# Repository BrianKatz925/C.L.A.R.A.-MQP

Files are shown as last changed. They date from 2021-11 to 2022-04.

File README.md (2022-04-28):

# C.L.A.R.A.-MQP

This is the GitHub repository for the 2021-22 CLARA MQP.

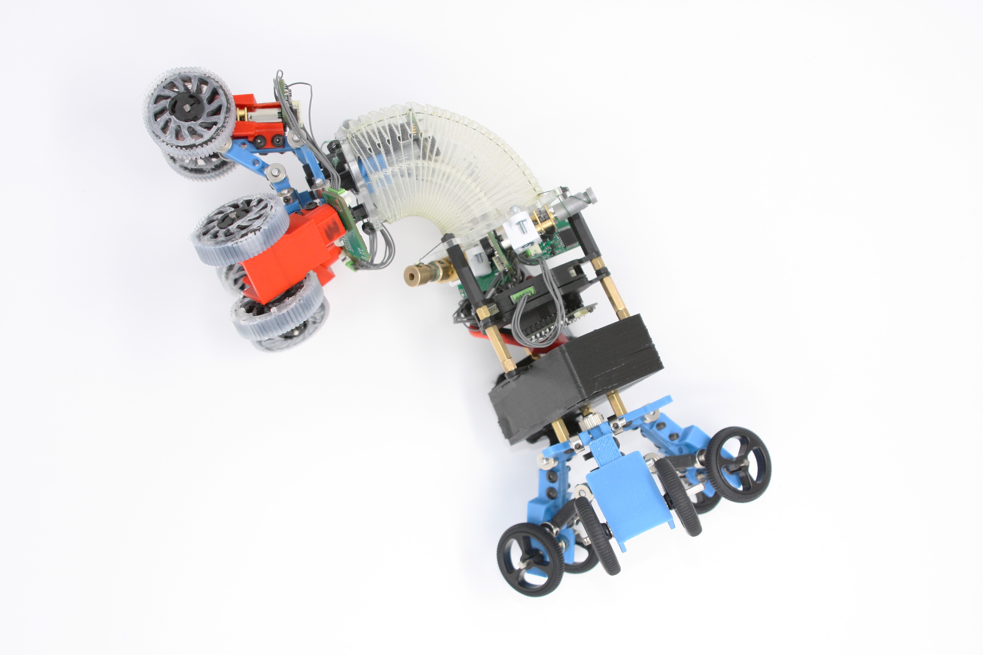
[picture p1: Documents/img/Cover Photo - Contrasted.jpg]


## Navigating the Repository
There are three main sections to the CLARA repository. 
  1. The first is the [Code](Code/) section, which contains all of the code used for the CLARA robot. Please refer to the [README](Code/README.md) in that section for more information on operation and code organization.
  2. The next is the [Documents](Documents/) section. In here, you can find all of the deliverables (presentation, report, etc.) and important planning documents used throughout our project.
  3. The last is the [Mechanical + Electrical Files](https://github.com/BrianKatz925/C.L.A.R.A.-MQP/tree/master/Mechanical%20%2B%20Electrical%20Files) section, which includes the Solidworks parts/assemblies, STLs, DXFs, and Altium Designer project files for the PCBs. Please refer to the [README](https://github.com/BrianKatz925/C.L.A.R.A.-MQP/blob/master/Mechanical%20%2B%20Electrical%20Files/README.md) in that section for more information on organization schema of the mechanical and electrical files.

Enjoy :)



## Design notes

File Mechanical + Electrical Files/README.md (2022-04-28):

# C.L.A.R.A.-MQP

This section contains all of the electrical and mechanical files for the 2021-22 CLARA MQP

## Navigating the this section
### PCB Files
In the [Altium](https://github.com/BrianKatz925/C.L.A.R.A.-MQP/tree/master/Mechanical%20%2B%20Electrical%20Files/Altium) section, you can find all iterations of the Mainboard and Smart Motor Driver PCB. The [Version 4 folder](https://github.com/BrianKatz925/C.L.A.R.A.-MQP/tree/master/Mechanical%20%2B%20Electrical%20Files/Altium/Version%204) contains the most updated version of each board.
  1. In the Version 4 folder, the main documents are the [CLARA Mainboard folder](https://github.com/BrianKatz925/C.L.A.R.A.-MQP/tree/master/Mechanical%20%2B%20Electrical%20Files/Altium/Version%204/CLARA%20Mainboard) and the [updated_sami_board_v3 folder](https://github.com/BrianKatz925/C.L.A.R.A.-MQP/tree/master/Mechanical%20%2B%20Electrical%20Files/Altium/Version%204/updated_sami_board%20v3/updated_sami_board).
  2. To import both of these files, along with other files in the design project in Altium, use the [Revision 4 12.24.2021.DsnWrk](https://github.com/BrianKatz925/C.L.A.R.A.-MQP/blob/master/Mechanical%20%2B%20Electrical%20Files/Altium/Version%204/Revision%204%2012.24.2021.DsnWrk) which will open up the design project group in Altium.

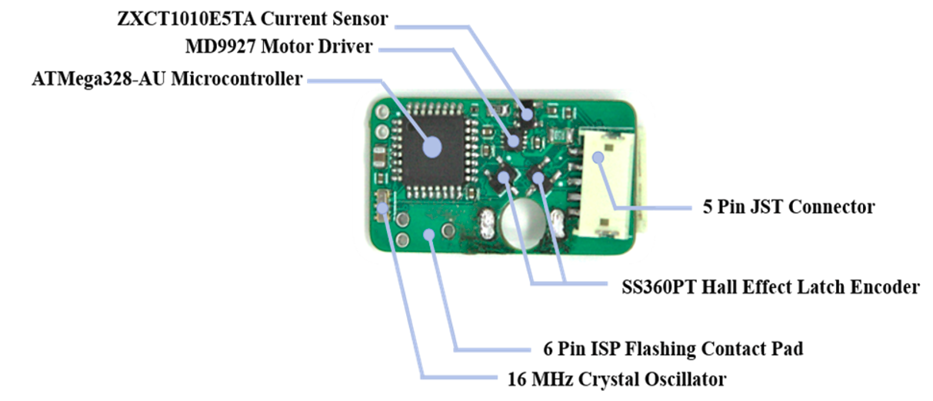
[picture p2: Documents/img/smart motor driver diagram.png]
|  | 
|:--:| 
| *Smart Motor Driver Diagram* |

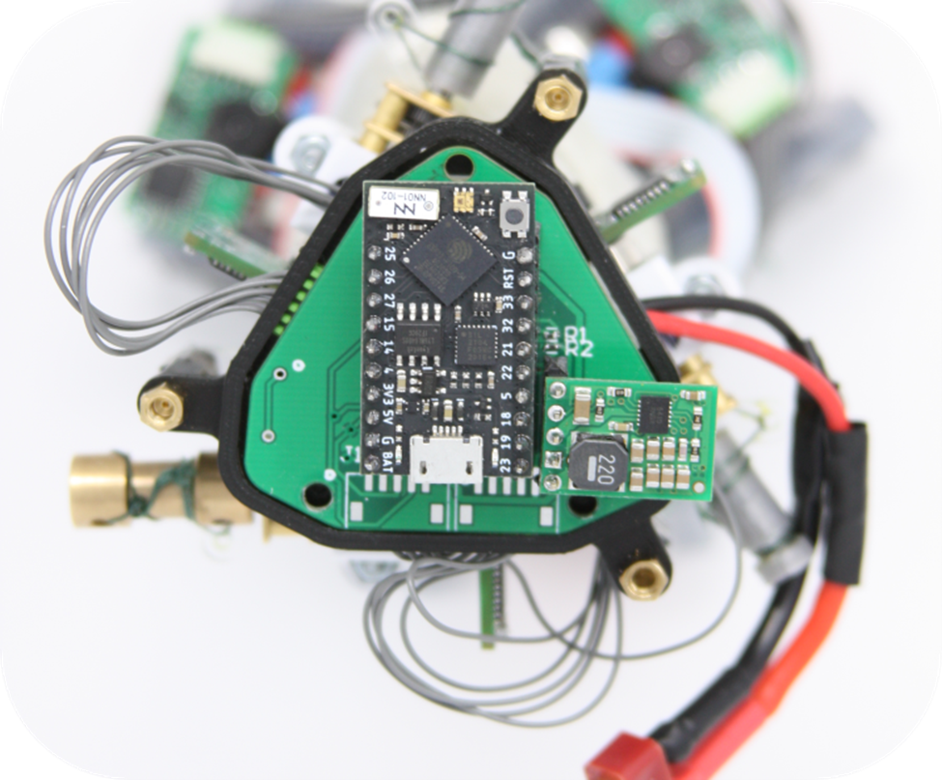
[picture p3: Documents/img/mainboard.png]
|  | 
|:--:| 
| *CLARA Mainboard* |

### Solidworks Files
In the [Salamander Assembly](https://github.com/BrianKatz925/C.L.A.R.A.-MQP/tree/master/Mechanical%20%2B%20Electrical%20Files/Salamander%20Assembly) folder, you will find the [Final CLARA Assembly](https://github.com/BrianKatz925/C.L.A.R.A.-MQP/blob/master/Mechanical%20%2B%20Electrical%20Files/Salamander%20Assembly/Final%20CLARA%20Assembly.ziphttps://github.com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) zip file, which is a pack-and-go from the final Solidworks Assembly.
  1. There is also a folder called [Final Version](https://github.com/BrianKatz925/C.L.A.R.A.-MQP/tree/master/Mechanical%20%2B%20Electrical%20Files/Salamander%20Assembly/Final%20Version) which contains some STL files as well. We recommend unzipping the pack-and-go as all files are included properly there.
  2. The [Alternative Version folder](https://github.com/BrianKatz925/C.L.A.R.A.-MQP/tree/master/Mechanical%20%2B%20Electrical%20Files/Salamander%20Assembly/Alternative%20Version) features our CAM-slide mechanism.
  3. The [Wheel Files folder](https://github.com/BrianKatz925/C.L.A.R.A.-MQP/tree/master/Mechanical%20%2B%20Electrical%20Files/Salamander%20Assembly/Wheel%20Files) features our wheel molds to create the TPU/Silicone compression wheels.
  4. Lastly, the [STL](https://github.com/BrianKatz925/C.L.A.R.A.-MQP/tree/master/Mechanical%20%2B%20Electrical%20Files/Salamander%20Assembly/STL) folder contains some of the STL files we used throughout the project for 3D printing.

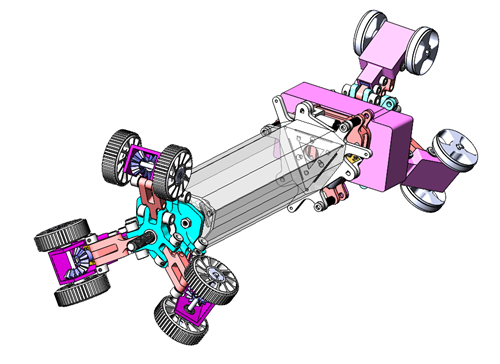
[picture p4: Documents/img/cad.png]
|  | 
|:--:| 
| *Final CAD Assembly of the CLARA Robot* |

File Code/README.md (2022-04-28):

# C.L.A.R.A.-MQP

This is the GitHub repository for the 2021-22 CLARA MQP.

## Instructions
### Prerequisites

1. Complete the prerequisites of the [CLARA-Gamepad Repository](https://github.com/phonymacoroni/CLARA-Gamepad).
2. Connect an ESP32 device (ESP32DevKitC, TinyPICO, etc.) to a USB port on your computer, this will be referred as the external ESP.
4. Upload the [`mac_address.ino` code](TinyPICO_Sender_Code/mac_address) to the external ESP and open the Serial Monitor, write down the MAC address.
5. Locate the [robotcode folder](robotcode), which contains the code required to operate the robot.
6. In the `pico_master.ino` and `inverse_kinematics_pico_master.ino` file, replace the current MAC address with that of the external ESP.
7. Connect the TinyPICO that will be going into the mainboard and retrieve its MAC address by repeating step 3.
8. In the `pico_sender.ino` and `inverse_kinematics_esp_sender.ino` files, replace the current MAC address with that of your TinyPICO.
9. For normal robot operation, upload the `pico_sender.ino code` to the external ESP and the `pico_master.ino` code to the mainboard TinyPICO.
10. For inverse kinematics demonstration, upload the `inverse_kinematics_esp_sender.ino` code to the external ESP and the `inverse_kinematics_pico_master.ino` to the mainboard TinyPICO.

### Operation
#### Typical Robot Operation
Typical Robot Operation requires the use of an external Logitech Gamepad as the form of input.

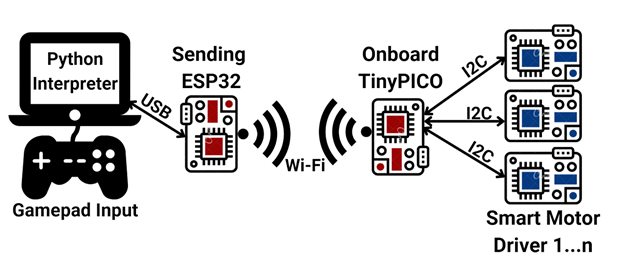
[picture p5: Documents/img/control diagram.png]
|  | 
|:--:| 
| *CLARA Operation Control Diagram* |

Refer to the control protocol for the Gamepad below:

| Input  | WiFi Sender Command  | I2C Status Command | Smart Motor Driver Action |
|:---:|:---:|:-----:|:-----:|
| Default | "0" | 0 | Brake all motors | 
| Y Button | "1" | 1 | Rotate lead screw (0x07) - increase diameter |
| X Button | "2" | N/A | Request encoder, current sensor, motor rpm data from all motors |
| A Button | "4" | 2 | Rotate lead screw (0x07) - decrease diameter |
| Right Bumper | "8" | 8 | Drive wheel motors forward - fast speed |
| Left Bumper | "9" | 9 | Drive wheel motors reverse - fast speed |
| DPad 0 (North) | "10" | 0 | Brake all motors - homing |
| DPad 1 (Northeast) | "11" | N/A | Decrease all cable lengths |
| DPad 2 (East) | "12" | Cable 1: 12, <br />Cable 2: 0, <br />Cable 3: 0 | Decrease cable 1 (0x04) length |
| DPad 3 (Southeast) | "13" | Cable 1: 12, <br />Cable 2: 12, <br />Cable 3: 0 | Decrease cable 1 (0x04) and cable 2 (0x05) length |
| DPad 4 (South) | "14" | Cable 1: 0, <br />Cable 2: 12, <br />Cable 3: 0 | Decrease cable 2 (0x05) length |
| DPad 5 (Southwest) | "15" | Cable 1: 0, <br />Cable 2: 12, <br />Cable 3: 12 | Decrease cable 2 (0x05) and cable 3 (0x06) length |
| DPad 6 (West) | "16" | Cable 1: 0, <br />Cable 2: 0, <br />Cable 3: 12 | Decrease cable 3 (0x06) length |
| DPad 7 (Northwest) | "17" | N/A | Increase all cable lengths |
| B Button + D Pad 2 | "18" | Cable 1: 13, <br />Cable 2: 0, <br />Cable 3: 0 | Increase cable 1 (0x04) length |
| B Button + D Pad 4 | "19" | Cable 1: 0, <br />Cable 2: 13, <br />Cable 3: 0 | Increase cable 2 (0x05) length |
| B Button + D Pad 6 | "20" | Cable 1: 0, <br />Cable 2: 0, <br />Cable 3: 13 | Increase cable 3 (0x06) length |
| B Button + Right Bumper | "21" | 10 | Drive wheel motors forward - PID slow speed |
| B Button + Right Bumper | "22" | 11 | Drive wheel motors reverse - PID slow speed|
| A Button + Right Bumper | "23" | 3 | Rotate lead screw (0x07) - decrease diameter until current limit |
| Y  Button + Right Bumper | "24" | 4 | Rotate lead screw (0x07) - increase diameter until current limit|

#### Inverse Kinematics Demonstration
The Gamepad can be disconnected with this demonstration.

Instead the Serial Monitor is used to input values for the configuration parameters **S** (arc length), **theta** (bending angle), and **phi** (rotation about z-axis).

The bounds for each variable are defined in the `inverse_kinematics_esp_sender.ino` file.

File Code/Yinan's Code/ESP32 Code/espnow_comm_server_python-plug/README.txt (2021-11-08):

Upload to the external ESP32 as the sender of messages

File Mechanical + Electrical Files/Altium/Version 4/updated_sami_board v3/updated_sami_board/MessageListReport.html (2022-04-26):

Altium customize

# Message List

Date: | | 10/12/2021
Time: | | 12:13:04 PM
Elapsed Time: | | 00:00:00

Class | Document | Source | Message | Time | Date | No.
Situs Event | sami_updated.PcbDoc | Situs | Routing Started | 12:12:19 PM | 10/12/2021 | 1
Routing Status | sami_updated.PcbDoc | Situs | Creating topology map | 12:12:19 PM | 10/12/2021 | 2
Situs Event | sami_updated.PcbDoc | Situs | Starting Fan out to Plane | 12:12:19 PM | 10/12/2021 | 3
Situs Event | sami_updated.PcbDoc | Situs | Completed Fan out to Plane in 0 Seconds | 12:12:19 PM | 10/12/2021 | 4
Situs Event | sami_updated.PcbDoc | Situs | Starting Memory | 12:12:19 PM | 10/12/2021 | 5
Situs Event | sami_updated.PcbDoc | Situs | Completed Memory in 0 Seconds | 12:12:19 PM | 10/12/2021 | 6
Situs Event | sami_updated.PcbDoc | Situs | Starting Layer Patterns | 12:12:19 PM | 10/12/2021 | 7
Routing Status | sami_updated.PcbDoc | Situs | Calculating Board Density | 12:12:19 PM | 10/12/2021 | 8
Situs Event | sami_updated.PcbDoc | Situs | Completed Layer Patterns in 0 Seconds | 12:12:19 PM | 10/12/2021 | 9
Situs Event | sami_updated.PcbDoc | Situs | Starting Main | 12:12:19 PM | 10/12/2021 | 10
Routing Status | sami_updated.PcbDoc | Situs | 58 of 60 connections routed (96.67%) in 19 Seconds 1 contention(s) | 12:12:38 PM | 10/12/2021 | 11
Situs Event | sami_updated.PcbDoc | Situs | Completed Main in 19 Seconds | 12:12:39 PM | 10/12/2021 | 12
Situs Event | sami_updated.PcbDoc | Situs | Starting Completion | 12:12:39 PM | 10/12/2021 | 13
Routing Status | sami_updated.PcbDoc | Situs | 59 of 60 connections routed (98.33%) in 34 Seconds | 12:12:53 PM | 10/12/2021 | 14
Situs Event | sami_updated.PcbDoc | Situs | Completed Completion in 14 Seconds | 12:12:53 PM | 10/12/2021 | 15
Situs Event | sami_updated.PcbDoc | Situs | Starting Straighten | 12:12:53 PM | 10/12/2021 | 16
Routing Status | sami_updated.PcbDoc | Situs | 59 of 60 connections routed (98.33%) in 35 Seconds | 12:12:54 PM | 10/12/2021 | 17
Situs Event | sami_updated.PcbDoc | Situs | Completed Straighten in 1 Second | 12:12:55 PM | 10/12/2021 | 18
Routing Status | sami_updated.PcbDoc | Situs | 59 of 60 connections routed (98.33%) in 36 Seconds | 12:12:55 PM | 10/12/2021 | 19
Situs Event | sami_updated.PcbDoc | Situs | Routing finished with 0 contentions(s). Failed to complete 1 connection(s) in 36 Seconds | 12:12:55 PM | 10/12/2021 | 20

Back to top

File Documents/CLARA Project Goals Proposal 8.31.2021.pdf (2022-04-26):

MQP Meeting #1
8.31.2021
Overview:
We would like to focus on primarily mechanical and electrical improvements to the existing salamander robot such that we can create a robot with the following specifications capable of performing the below demonstrations. Additionally, we would like to tailor the improvements and constraints in order to qualify the robot for the NASA Big Idea Challenge, and work with another MQP team as necessary in order to meet the mechanical, electrical, and controls requirements of the challenge.

Areas of Interest:
- Improved suspension system. Want to use either a passively or actively deformable suspension system to make the robot capable of traversing multiple sized tubes
- Improved PCB design. Want a new PCB design that is smaller overall (whether that be through enhanced PCB space allocation or a foldable/flexible board) and allows us to scale down the size of the body
- Viability of smaller body with either the Yoshimura pattern or another folding pattern still capable of deforming linearly while maintaining the present level of torsional stiffness
- Integrating usage of robot with vine soft robot for deployment purposes as well as making the salamander usable in wet/humid environments
- Making robot usable in both vacuum and pressurized environments

Specifications:
- Size
- Robot should be able to be used within a 3” SCH STD pipe
■ Due to schedule piping, the ID of a 2” ND pipe would be below 2” and the 3” ND pipe will be >2”.
- Robot is usable in pipes up to 6” nominal for vertical climbs
- Speed
- Robot is able to travel at a reasonable pace (this will be hardware dependant)
- Mobility
- Robot should meet a 90 degree minimum turning radius
- Robot should be able to traverse a 90 degree incline in a pipe
- Robot should be able to climb at least a 30 degree slope.
- Robot should be able to traverse pipe with constrictions/expansion
■ This would be doable with an active suspension, not so much with a passive unless we have enough force to really push the robot forward to where the suspension system buckles inward
- Sensing
- Robot should be, at minimum, able to integrate a camera at the robot head for navigation/inspection/sample collection purposes
- We’re gonna need other sensing? Temperature and Pressure sensors might be good and easy, if we care about mapping the space this gets more complex
- Other
- Robot should be able to deploy a small scientific payload ( idk what size that really means here)

■ This might mean we have to have a modular design of the robot, so that we can have a scoop or something to collect regolith

Demonstrations:
- Within clear pipe
- General locomotion
■ Forwards, turning, etc.
- Passage through a t-split
■ Choose which direction to take instead of following flow
- Locomotion through varying inclines (45, 60, 90?)
■ Within pipes and potentially up stairs
- Traverse a constriction
- Bridge a gap
■ To deploy the robot into a pipe inlet without human assistance
- Deployment with vine robot
- Can we actually get our hands on one? It may be hard to really demonstrate this otherwise
- Payload deployment

Questions
- Budget
- If our budget is low, do you have any recommendations for receiving funding?
- Lab space/equipment
- Do we have a dedicated lab space (Soft Robotics Lab), if so can we get Kate access?
- Start to set calendar/Gantt chart with major deadlines that we currently know of

A Term Goals
By end of A term we have:
- Made it through rapid prototyping phase of suspension mechanism - pursued at least 3 designs and tested physical models
- Gives us an outline for the overall maximum size and flexibility of the robot
- Have landed on a solution/have a solid plan for the smaller PCB. Doesn’t have to be completed, but we must land on a path forward
- Talk to Dan Moyer - get a consultation on the feasibility of a foldable/flexible PCB and what connections may be subtracted
- Will give minimum size
- Have a viable solution to the smaller body. Have either produced a smaller body with the current folding pattern or have found another solution.
- This will outline the minimum size

Other notes:
With regards to NASA challenge
- Market and sell robot as being good in steep and rugged slopes and for subterranean features (especially caves and lava tubes)
- Required:
- Needs to be able to manage intrusion of dust
- Be cost effective
- Low barrier to adoption. (i.e. low mass, small, low power, reliable)
- Desired
- Able to autonomously navigate through hazardous environments
- Able to transport objects with larger mass than it’s own

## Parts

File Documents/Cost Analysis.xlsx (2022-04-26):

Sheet: Sheet1
Category | Part Name | Quantity | Unit Cost | Extended Cost
Body
 | PET Sheet | 36"x10" sheet | $0.00 | $0.00
 | PowerPro 50lb fishing line | 18" | $20.00 | $0.03
 | Cable Winches | 3 | $0.00 | $0.00
 | Acrylic Mounting Plates | 2 | $0.00 | $0.00
 | Motor Brackets | 3 | $3.95 | $11.85
Suspension
 | 3D Printed Parts | - | $0.00 | $0.00
 | 5mm Ball Bearing | 3 | $1.00 | $3.00
 | 5mm Shaft Collar | 3 | $0.78 | $2.35
 | M5 Lead Screw (4") | 1 | $0.00 | $0.00
 | M3 Shaft Collar | 30 | $0.27 | $7.99
 | M3 Assorted Screw Kit | 1 | $10.98 | $10.98
 | 3mm Ball Bearing | 12 | $1.70 | $20.38
 | 3mm D Shaft | 20" | $0.00 | $0.00
 | Standoffs | 12 | $0.00 | $0.00
 | Dragonskin | 0.25 bottle | $0.00 | $0.00
 | Pololu Wheels | 12 | $1.48 | $17.70
Electronics
 | 1:150 N20 Gearmotor | 1 | $3.00 | $3.00
 | 1:298 N20 Gearmotor | 6 | $23.45 | $140.70
 | Smart Motor Drivers (components incl) | 7 | $9.32 | $65.23
 | Mainboard (components incl) | 1 | $34.08 | $34.08
 | Tiny Pico | 1 | $20.00 | $20.00
 | Buck Regulator | 1 | $6.95 | $6.95
 | ESP 32 | 1 | $9.00 | $9.00
 | 12 CPR Encoder Disks | 7 | $2.00 | $14.00
 | LiPo Battery | 1 | $10.95 | $10.95
 | 6 pin pogo connector | 1 | $33.95 | $33.95
 | Logitech Gamepad | 1 | $16.39 | $16.39
 | 6 cable JST connectors | 7 | $1.59 | $11.13
Total |  |  |  | $439.65

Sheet: Smart Motor Driver
Part Name | Qty ordered | total cost | cost per component | components per board | cost per board
PCB Board | 10 | $5.00 | $0.50 | 1 | $0.50
ATMega328-AU | 25 | $79.10 | $3.16 | 1 | $3.16
SS360PT Hall Effect Sensor | 20 | $22.20 | $1.11 | 2 | $2.22
MD9927 Motor Driver | 30 | $5.19 | $0.17 | 1 | $0.17
ZXCT1010E5TA Current Sensor | 30 | $22.51 | $0.75 | 1 | $0.75
GRM155R71C104KA88D 0.1 uF capacitor | 50 | $1.10 | $0.02 | 6 | $0.13
CSTNE16M0V53C000R0 16 MHz oscillator | 20 | $5.46 | $0.27 | 1 | $0.27
GRM21BR61E106KA73L 10 uF capacitor | 25 | $7.30 | $0.29 | 1 | $0.29
ERJ-1GNF1002C - 10 kOhm Resistor | 25 | $1.33 | $0.05 | 1 | $0.05
RL1220S-R50-F - 0.5 Ohm Resistor | 25 | $6.08 | $0.24 | 1 | $0.24
ERA-3AEB122V - 1.2 kOhm Resistor | 25 | $7.48 | $0.30 | 1 | $0.30
S5B-ZR-SM4A-TF(LF)(SN) 5 pin JST connector | 50 | $30.46 | $0.61 | 2 | $1.22
 |  |  |  | Total | $9.32

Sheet: Mainboard
Part Name | Qty ordered | total cost | cost per component | components per board | cost per board
PCB Board | 5 | $5.00 | $1.00 | 1 | $1.00
S5B-ZR-SM4A-TF(LF)(SN) 5 pin JST connector | 50 | $30.46 | $0.61 | 9 | $5.48
TinyPICO ESP32 Microcontroller | 3 | $60.00 | $20.00 | 1 | $20.00
D24V10F3 - 3.3 Buck Regulator | 2 | $14.98 | $7.49 | 1 | $7.49
RMCF0402JT4K70 - 10kOhm Resistor | 25 | $1.33 | $0.05 | 2 | $0.11
Dean's Connector | 5 | $9.49 | $1.90 | 2 | $3.80
 |  |  |  | Total | $34.08

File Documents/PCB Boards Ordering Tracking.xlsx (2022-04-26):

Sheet: Big Old - Sami
Component # | Description | QTY per board | Stock | Cost | Link | Total Required | Total Cost | Potential Replacement?
TLE4946-2K | Hall Effect Sensor | 2 | 384 | 0.27 - must buy all 384 | https://www.rocelec.com/part/inftle4946-2k |  |  | https://www.mouser.com/ProductDetail/Honeywell/SS360PT?qs=I6adikXrXuA6SFyXzjBzBQ%3D%3D
ATTINY2313V-10MU | 8-bit Microcontroller 18 I/O Pins | 1 | 1139 | 1.96 | https://www.mouser.com/ProductDetail/Microchip-Technology-Atmel/ATTINY2313V-10MU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
LT1999IMS8-20#PBF | Current Sense Amplifiers | 1 | 0 | 5.84 | https://www.mouser.com/ProductDetail/Analog-Devices/LT1999IMS8-20PBF?qs=ytflclh7QUVh4hf%252BhdZY6Q%3D%3D |  |  | 27 available from SRL
SM05B-GHS-TB(LF)(SN) | JST | 2 | 1707 | 0.5 | https://lcsc.com/product-detail/Wire-To-Board-Wire-To-Wire-Connector_JST-Sales-America-SM05B-GHS-TB-LF-SN_C189896.html

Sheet: 104 - Sami
Component # | Description | QTY per board | Stock | Cost | Link | Total Required | Total Cost | Potential Replacement?
SS360PT | Digital Hall Effect Sensor | 2 | 7062 | 1.7 | https://www.mouser.com/ProductDetail/Honeywell/SS360PT?qs=I6adikXrXuA6SFyXzjBzBQ%3D%3D
A3910EEETR-T | Half Bridge (2) DC Brushed Motor Driver | 1 | 11938 | 0.68 | https://www.digikey.com/en/products/detail/allegro-microsystems/A3910EEETR-T/3973532
? | 100 mOhm Resistor | 1 | - | -
INA2180A1IDGKR | Current Sense Amplifier | 1 | 3857 | 0.71 | https://www.mouser.com/ProductDetail/Texas-Instruments/INA2180A1IDGKR?qs=j%252B1pi9TdxUZfv9X7r5aZLA%3D%3D
GRM155R71C104KA88D | 0.1 uF Capacitor | 4 | 840141 | 0.1 | https://www.mouser.com/ProductDetail/Murata-Electronics/GRM155R71C104KA88D?qs=8YPuuxuUzMJKePo9sU3A2g%3D%3D
SM05B-GHS-TB(LF)(SN) | JST Connector | 2 | 1342 | 0.1747 | https://lcsc.com/product-detail/Wire-To-Board-Wire-To-Wire-Connector_JST-Sales-America-SM05B-GHS-TB-LF-SN_C189896.html
ATtiny2313V-10MU | 8 bit microcontroller | 1 | 1139 | 2.08 | https://www.mouser.com/ProductDetail/Microchip-Technology-Atmel/ATTINY2313V-10MU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
CSTNE16M0V53C000R0 | 16MHz Crystal | 1 | 43962 | 0.33 | https://www.digikey.com/en/products/detail/murata-electronics/CSTNE16M0V53C000R0/8747730

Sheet: 106 - Sami
Component # | Description | QTY per board | Stock | Cost | Link | Total Required | Total Cost | Potential Replacement?
SS360PT | Digital Hall Effect Sensor | 2 | 7062 | 1.7 | https://www.mouser.com/ProductDetail/Honeywell/SS360PT?qs=I6adikXrXuA6SFyXzjBzBQ%3D%3D
A3910EEETR-T | Half Bridge (2) DC Brushed Motor Driver | 1 | 11938 | 0.68 | https://www.digikey.com/en/products/detail/allegro-microsystems/A3910EEETR-T/3973532
INA2180A1IDGKR | Current Sense Amplifier | 1 | 3857 | 0.71 | https://www.mouser.com/ProductDetail/Texas-Instruments/INA2180A1IDGKR?qs=j%252B1pi9TdxUZfv9X7r5aZLA%3D%3D
GRM155R71C104KA88D | 0.1 uF Capacitor | 5 | 840141 | 0.1 | https://www.mouser.com/ProductDetail/Murata-Electronics/GRM155R71C104KA88D?qs=8YPuuxuUzMJKePo9sU3A2g%3D%3D
SM05B-GHS-TB(LF)(SN) | JST Connector | 2 | 1342 | 0.1747 | https://lcsc.com/product-detail/Wire-To-Board-Wire-To-Wire-Connector_JST-Sales-America-SM05B-GHS-TB-LF-SN_C189896.html
ATMEGA328-AU | 8 bit microcontroller | 1 | 2151 | 2.18 | https://www.mouser.com/ProductDetail/Microchip-Technology-Atmel/ATMEGA328-AU?qs=lwdSMh1%2FoYJRHuGBjWz9Pg%3D%3D | https://store.arduino.cc/products/arduino-nano
CSTNE16M0V53C000R0 | 16MHz Crystal | 1 | 43962 | 0.33 | https://www.digikey.com/en/products/detail/murata-electronics/CSTNE16M0V53C000R0/8747730
RL1220S-R10-F | 100 mOhm Resistor | 1 | 27890 | 0.29 | https://www.digikey.com/en/products/detail/susumu/RL1220S-R10-F/432480
JMF212AB7106KGHT | 10 uF Capacitor | 1 | 94430 | 0.3 | https://www.mouser.com/ProductDetail/Taiyo-Yuden/JMF212AB7106KGHT?qs=GedFDFLaBXGIGsv8E%252BcpMQ%3D%3D
ERJ-1GNF1002C - 10kOhm | 10 kOhm Resistor | 1 | 888637 | 0.1 | https://www.digikey.com/en/products/detail/panasonic-electronic-components/ERJ-1GNF1002C/2036226

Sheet: 106 - Mainboard
Component # | Description | QTY per board | Stock | Cost | Link | Total Required | Total Cost | Potential Replacement?
TinyPICO | ESP32 Controller | 1 | 1 | 20 | https://www.adafruit.com/product/4335 | 1 | 20
NCV1117ST50T3G | 5V Voltage Regulator | 1 | 6298 | 0.61 | https://www.digikey.com/en/products/detail/on-semiconductor/NCV1117ST50T3G/1967231 | 1
SM05B-GHS-TB(LF)(SN) | JST Connector | 9 | 837 | 0.17 | https://lcsc.com/product-detail/Wire-To-Board-Wire-To-Wire-Connector_JST-Sales-America-SM05B-GHS-TB-LF-SN_C189896.html | 9
NCP1117DT33T5G | 3.3V Voltage Regulator | 1 | 37696 | 0.58 | https://www.digikey.com/en/products/detail/onsemi/NCP1117DT33T5G/921285 | 1
JMF212AB7106KGHT | 10 uF Capacitor | 4 | 94430 | 0.3 | https://www.mouser.com/ProductDetail/Taiyo-Yuden/JMF212AB7106KGHT?qs=GedFDFLaBXGIGsv8E%252BcpMQ%3D%3D | 4
BM02B-SRSS-TB (LF)(SN) | 2 pin JST Connector | 1 | 36697 | 0.48 | https://www.digikey.com/en/products/detail/jst-sales-america-inc/BM02B-SRSS-TB-LF-SN/926694 | 1

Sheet: 1010 - Sami
Component # | Description | QTY per board | Stock | Cost | Link | In Hand
SS360PT | Digital Hall Effect Sensor | 2 | 7062 | 1.7 | https://www.mouser.com/ProductDetail/Honeywell/SS360PT?qs=I6adikXrXuA6SFyXzjBzBQ%3D%3D
A3910EEETR-T | Half Bridge (2) DC Brushed Motor Driver | 1 | 11938 | 0.68 | https://www.digikey.com/en/products/detail/allegro-microsystems/A3910EEETR-T/3973532 | 10
INA2180A1IDGKR | Current Sense Amplifier | 1 | 3857 | 0.71 | https://www.mouser.com/ProductDetail/Texas-Instruments/INA2180A1IDGKR?qs=j%252B1pi9TdxUZfv9X7r5aZLA%3D%3D
GRM155R71C104KA88D | 0.1 uF Capacitor | 7 | 840141 | 0.1 | https://www.mouser.com/ProductDetail/Murata-Electronics/GRM155R71C104KA88D?qs=8YPuuxuUzMJKePo9sU3A2g%3D%3D
S5B-ZR-SM4A-TF(LF)(SN) | JST Connector - ZR Family | 2 | 25147 | 0.1747 | https://www.digikey.com/en/products/detail/jst-sales-america-inc/S5B-ZR-SM4A-TF-LF-SN/926603
ATMEGA328-AU | 8 bit microcontroller | 1 | 2151 | 2.18 | https://www.mouser.com/ProductDetail/Microchip-Technology-Atmel/ATMEGA328-AU?qs=lwdSMh1%2FoYJRHuGBjWz9Pg%3D%3D
CSTNE16M0V53C000R0 | 16MHz Crystal | 1 | 43962 | 0.33 | https://www.digikey.com/en/products/detail/murata-electronics/CSTNE16M0V53C000R0/8747730 | 10
GRM21BR61E106KA73L | 10 uF Capacitor | 1 | 2941945 | 0.42 | https://www.digikey.com/en/products/detail/murata-electronics/GRM21BR61E106KA73L/2334874
ERJ-1GNF1002C - 10kOhm | 10 kOhm Resistor | 1 | 888637 | 0.1 | https://www.digikey.com/en/products/detail/panasonic-electronic-components/ERJ-1GNF1002C/2036226 | 25
RL1220S-R27-F | 0.27 Ohm Resistor | 1 | 270043 | 0.29 | https://www.digikey.com/en/products/detail/susumu/RL1220S-R27-F/714262 | 0

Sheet: 1010 - Mainboard
Component # | Description | QTY per board | Stock | Cost | Link | Total Required | In Hand
TinyPICO | ESP32 Controller | 1 | 1 | 20 | https://www.adafruit.com/product/4335 | 1
S5B-ZR-SM4A-TF(LF)(SN) | JST Connector - ZR Family | 9 | 25147 | 0.1747 | https://www.digikey.com/en/products/detail/jst-sales-america-inc/S5B-ZR-SM4A-TF-LF-SN/926603 | 9
NCP1117DT33T5G | 3.3V Voltage Regulator | 1 | 37696 | 0.58 | https://www.digikey.com/en/products/detail/onsemi/NCP1117DT33T5G/921285 | 1 | 5
GRM21BR61E106KA73L | 10 uF Capacitor | 2 | 2941945 | 0.42 | https://www.digikey.com/en/products/detail/murata-electronics/GRM21BR61E106KA73L/2334874 | 4 | 25
BM02B-SRSS-TB (LF)(SN) | 2 pin JST Connector | 1 | 36697 | 0.48 | https://www.digikey.com/en/products/detail/jst-sales-america-inc/BM02B-SRSS-TB-LF-SN/926694 | 1 | 10
RMCF0402JT4K70 | 4.7 kOhm Resistor | 2 |  | 0.1 | https://www.digikey.com/en/products/detail/stackpole-electronics-inc/RMCF0402JT4K70/1758241 |  | 25
A05ZR05ZR28H102A | JST ZR Cable - 4" | 10 | 9389 | 1.38 | https://www.digikey.com/en/products/detail/A05ZR05ZR28H102A/455-4306-ND/9972177?so=72195384
A05ZR05ZR28H305B | JST ZR Cable - 12" | 5 | 578 | 1.88 | https://www.digikey.com/en/products/detail/A05ZR05ZR28H305B/455-4249-ND/6708565?so=72195384

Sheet: Things Left To Order
Component # | Description | QTY per board | Stock | Cost | Link | Total Required | In Hand
TC2030-IDC-NL | 6 Pin Spring Loaded Flashing Cable | 1 |  | 33.95 | https://www.tag-connect.com/product/tc2030-idc-nl | 1
Lithium Ion Battery - 3.7v 2000mAh |  | 1 |  | 12.5 | https://www.adafruit.com/product/2011 | 1

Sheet: 1121 - SAMI
Component # | Description | QTY per board | Stock | Cost | Link | In Hand | Reimbursement Sent? | Future Order | Ordered? | Reimbursement Sent?
SS360PT | Digital Hall Effect Sensor | 2 | 6886 | 1.7 | https://www.mouser.com/ProductDetail/Honeywell/SS360PT?qs=I6adikXrXuA6SFyXzjBzBQ%3D%3D | 20 | Yes | 10
GRM155R71C104KA88D | 0.1 uF Capacitor | 7 | 1526282 | 0.1 | https://www.mouser.com/ProductDetail/Murata-Electronics/GRM155R71C104KA88D?qs=8YPuuxuUzMJKePo9sU3A2g%3D%3D | 50 | Yes | 50
S5B-ZR-SM4A-TF(LF)(SN) | JST Connector - ZR Family | 2 | 22893 | 0.1747 | https://www.digikey.com/en/products/detail/jst-sales-america-inc/S5B-ZR-SM4A-TF-LF-SN/926603 | 25 | Yes | 20
ATMEGA328-AU | 8 bit microcontroller | 1 | 0 Fuck Chip Shortage | 2.18 | https://www.mouser.com/ProductDetail/Microchip-Technology-Atmel/ATMEGA328-AU?qs=lwdSMh1%2FoYJRHuGBjWz9Pg%3D%3D | 10 | Yes | 15 | Yes from RFQ | No
CSTNE16M0V53C000R0 | 16MHz Crystal | 1 | 0 | 0.33 | https://www.digikey.com/en/products/detail/murata-electronics/CSTNE16M0V53C000R0/8747730 | 10 | Yes | 12 | Yes | No
GRM21BR61E106KA73L | 10 uF Capacitor | 1 | 2941945 | 0.42 | https://www.digikey.com/en/products/detail/murata-electronics/GRM21BR61E106KA73L/2334874 | 25 | Yes | No
ERJ-1GNF1002C - 10kOhm | 10 kOhm Resistor | 1 | 888637 | 0.1 | https://www.digikey.com/en/products/detail/panasonic-electronic-components/ERJ-1GNF1002C/2036226 | 25 | Yes | No
---------
MD9927 | H-Bridge Motor Driver supports 8.4V | 1 | 27 | 0.25 | https://www.lcsc.com/product-detail/Motor-Driver-ICs_Shanghai-Mingda-Microelectronics-MD9927_C2684662.html | 0 | No | 30 | Yes | No
ZXCT1010E5TA | Current Sense Amplifier - 20 V | 1 | 20 | 1.04 | https://www.lcsc.com/product-detail/Current-Sensing-Amplifiers_Diodes-Incorporated-ZXCT1010E5TA_C14151.html | 0 | No | 30 | Yes | No
ERA-3AEB122V | 1.2KOhm Resistor - 1/10W 0603 | 1 | 55813 | 0.32 | https://www.digikey.com/en/products/detail/panasonic-electronic-components/ERA-3AEB122V/1465856 | 0 | No | 30
RL1220S-R50-F | 0.5 Ohm Resistor - 1/3W 0805 | 1 | 2957 | 0.29 | https://www.digikey.com/en/products/detail/susumu/RL1220S-R50-F/567251 | 0 | No | 30

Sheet: 1121 Mainboard
Component # | Description | QTY per board | Stock | Cost | Link | In Hand | Reimbursement Request Sent? | Future Order
TinyPICO | ESP32 Controller | 1 | 1 | 20 | https://www.adafruit.com/product/4335 | 2 | Yes
S5B-ZR-SM4A-TF(LF)(SN) | JST Connector - ZR Family | 9 | 22893 | 0.1747 | https://www.digikey.com/en/products/detail/jst-sales-america-inc/S5B-ZR-SM4A-TF-LF-SN/926603 | 25 | Yes | 20
GRM21BR61E106KA73L | 10 uF Capacitor | 2 | 2941945 | 0.42 | https://www.digikey.com/en/products/detail/murata-electronics/GRM21BR61E106KA73L/2334874 | 25 | Yes | 30
BM02B-SRSS-TB (LF)(SN) | 2 pin JST Connector | 1 | 36697 | 0.48 | https://www.digikey.com/en/products/detail/jst-sales-america-inc/BM02B-SRSS-TB-LF-SN/926694 | 10 | Yes | No
RMCF0402JT4K70 | 4.7 kOhm Resistor | 2 | 1947472 | 0.1 | https://www.digikey.com/en/products/detail/stackpole-electronics-inc/RMCF0402JT4K70/1758241 | 25 | Yes | No
A05ZR05ZR28H102A | JST ZR Cable - 4" | 10 | 9389 | 1.38 | https://www.digikey.com/en/products/detail/A05ZR05ZR28H102A/455-4306-ND/9972177?so=72195384 | 10 | Yes | No
A05ZR05ZR28H305B | JST ZR Cable - 12" | 5 | 578 | 1.88 | https://www.digikey.com/en/products/detail/A05ZR05ZR28H305B/455-4249-ND/6708565?so=72195384 | 5 | Yes | No
Lithion Ion Battery 3.7V + Micro USB Charger |  | 1 | - | 31.32 |  | 1 | No | No
Tag Connect 6 Pin ISP Connector |  | 1 |  | 33.95 |  | 1 | No | No
---
D24V10F3 | Pololu 3.3V Buck Switching Regulator Module | 1 | 81 | 7.49 | https://www.pololu.com/product/2830 | 0 |  | 2

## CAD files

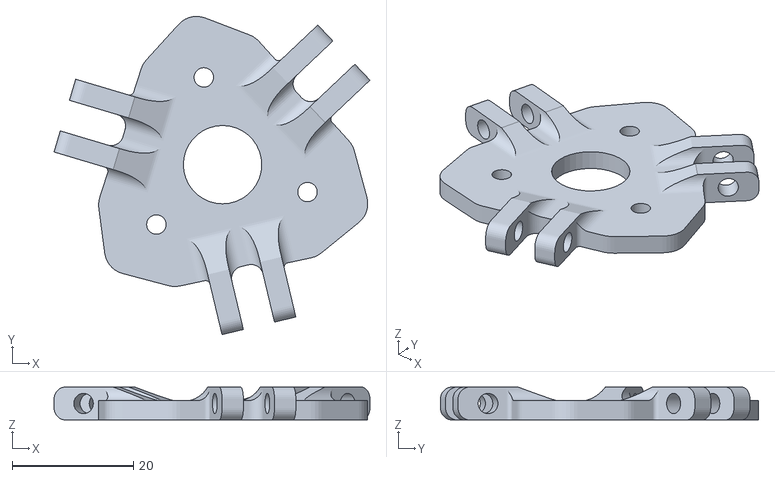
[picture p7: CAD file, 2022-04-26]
Mechanical + Electrical Files/Salamander Assembly/Final Version/STL/Bottom Link Faceplate^Salamander Assembly.STL
52.0 x 52.4 x 5.43

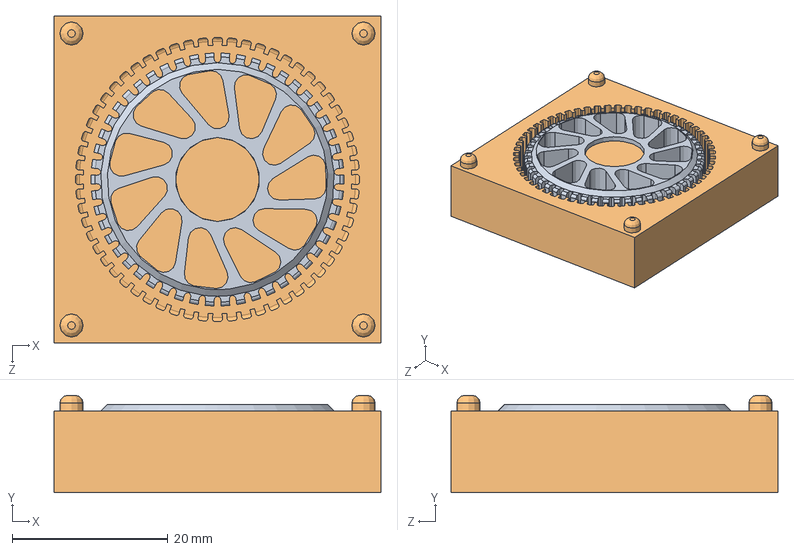
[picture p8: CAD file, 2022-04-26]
Mechanical + Electrical Files/Salamander Assembly/Wheel Files/Mold v2/Moldyv2.SLDASM
42.0 x 12.5 x 42.0 mm
COmpression Wheel v5
Cavityv2

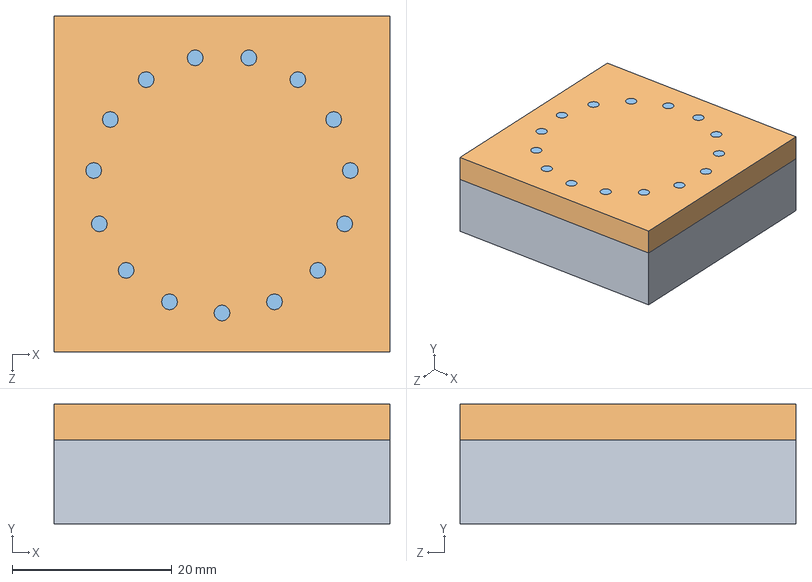
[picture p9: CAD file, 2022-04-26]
Mechanical + Electrical Files/Salamander Assembly/Wheel Files/Mold v2/Mold Assemv2.SLDASM
42.0 x 14.9 x 42.0 mm
Cavityv2
Cavity No Cavityv2

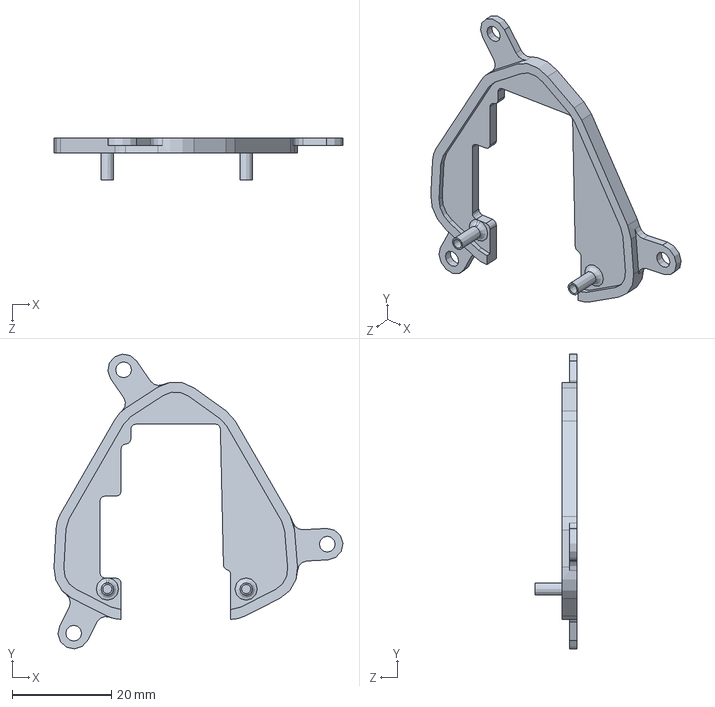
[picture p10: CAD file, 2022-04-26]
Mechanical + Electrical Files/Salamander Assembly/Final Version/Mainboard Shell Top.SLDPRT
58.3 x 59.5 x 8.50 mm

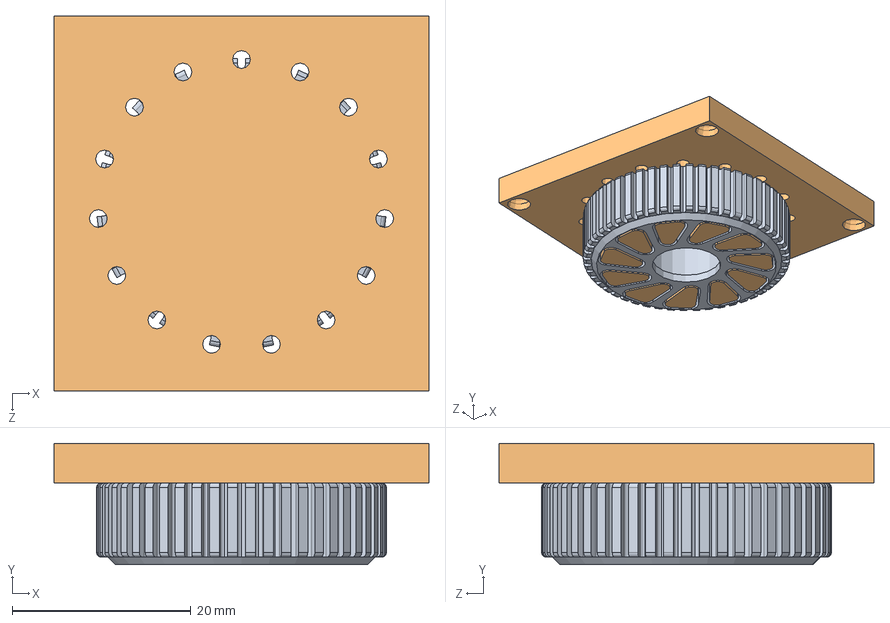
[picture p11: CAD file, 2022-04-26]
Mechanical + Electrical Files/Salamander Assembly/Wheel Files/Mold v2/Moldy2v2.SLDASM
42.0 x 13.6 x 42.0 mm

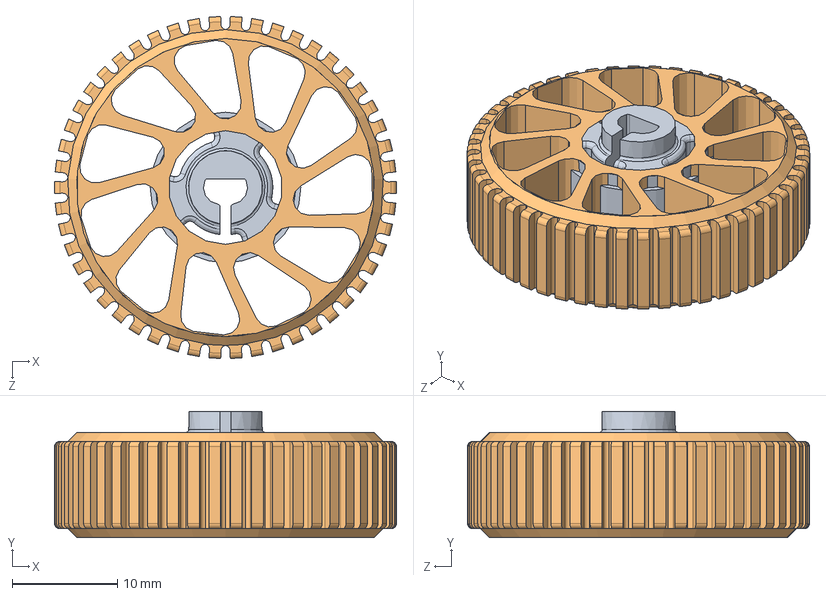
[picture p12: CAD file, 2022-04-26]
Mechanical + Electrical Files/Salamander Assembly/Wheel Files/Compression Wheel v6.SLDASM
32.5 x 12.0 x 32.5 mm
Outer Wheel v3
COmpression Wheel v5

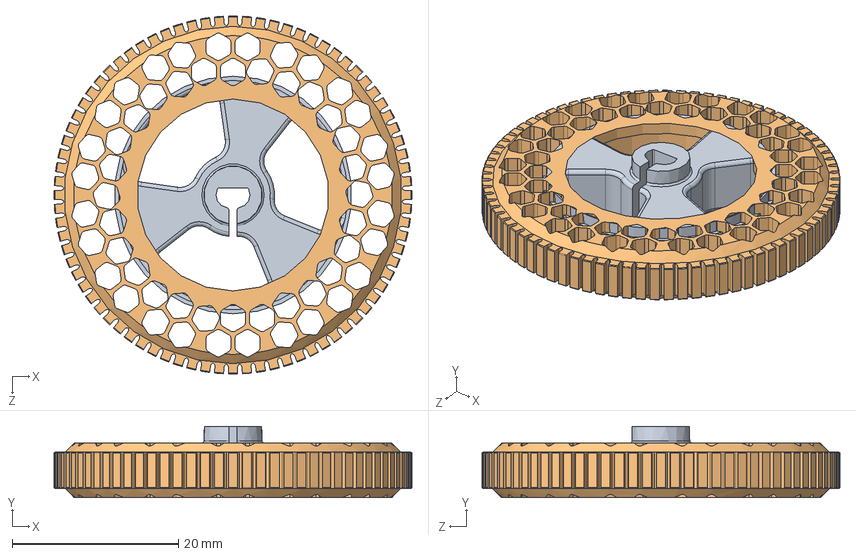
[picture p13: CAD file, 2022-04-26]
Mechanical + Electrical Files/Salamander Assembly/Wheel Files/Compression Wheel.SLDASM
43.1 x 8.60 x 43.1 mm
Outer Wheel
Part1^Compression Wheel

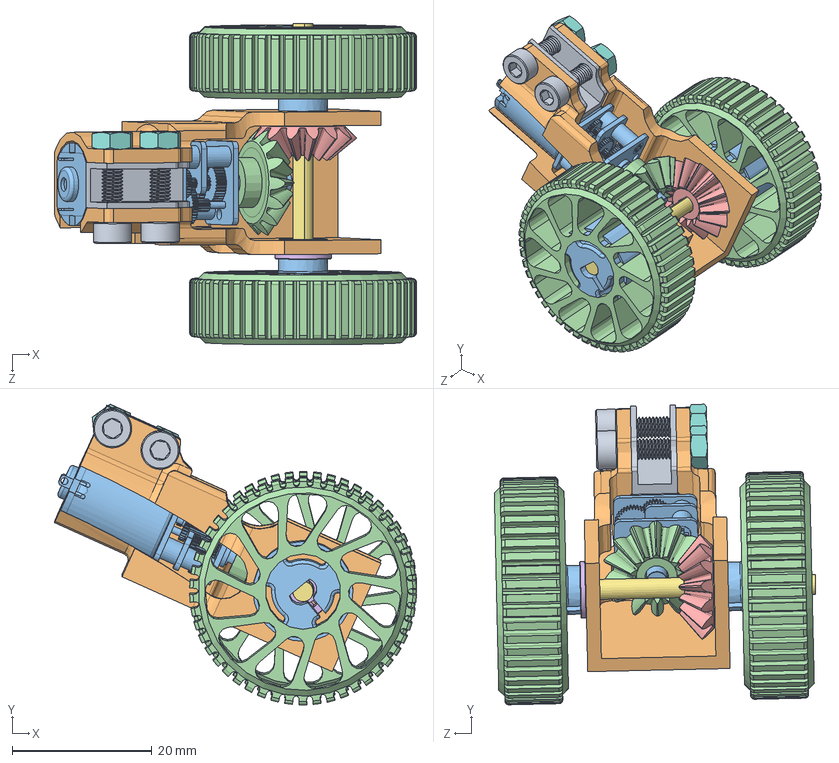
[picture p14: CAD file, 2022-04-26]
Mechanical + Electrical Files/Salamander Assembly/Alternative Version/Motor Housing 1.SLDASM
51.8 x 43.1 x 46.0 mm
Motor Base2
Motor Mount
micro-metal-gearmotor
With_convex-Metric - Straight miter gear 1M14T 20PA 5FW
Metric - Straight miter gear 1M14T 20PA 5FW ---14O10H8MD2N
57155K427_Stainless Steel Ball Bearing x 2
Dshaftd3l40
90592A085_STEEL HEX NUT x 2
91290A115_Black-Oxide Alloy Steel Socket Head Screw x 2
Bevel Gear Spacer
Outer Wheel v3 x 2
COmpression Wheel v5 x 2

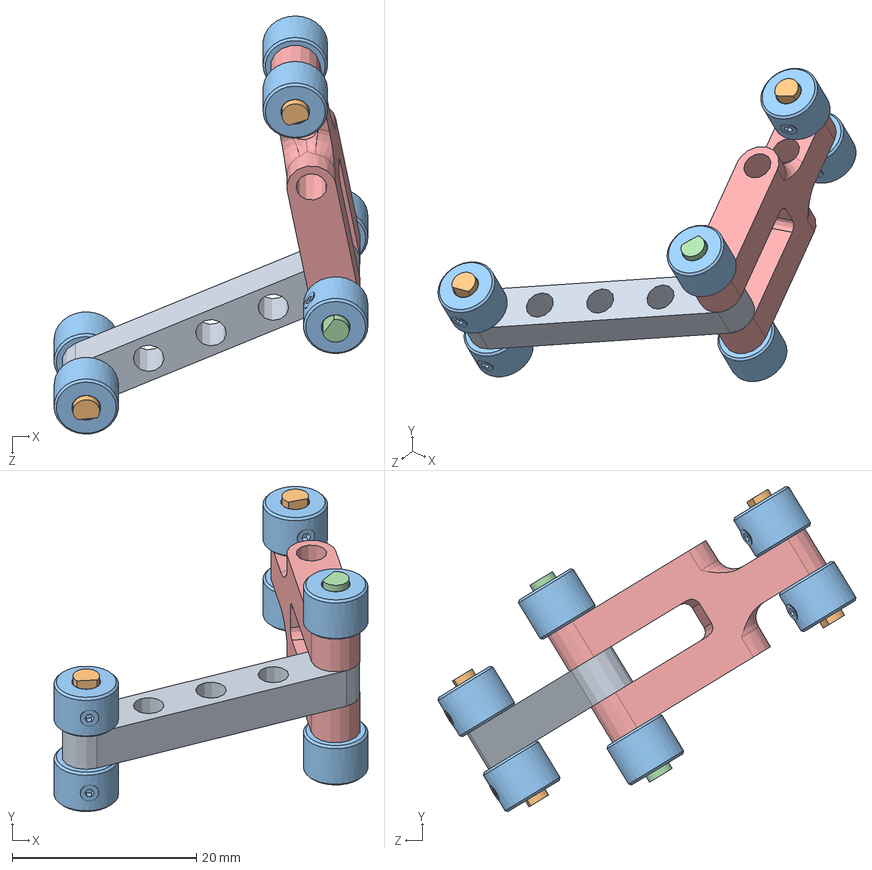
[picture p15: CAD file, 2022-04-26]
Mechanical + Electrical Files/Salamander Assembly/Final Version/Link Assembly.SLDASM
34.1 x 35.3 x 45.4 mm
Base Link
Aluminum D Shaft x 2
6056N11_Carbon Steel Set Screw Collar x 6
Link D Shaft
Upper Link

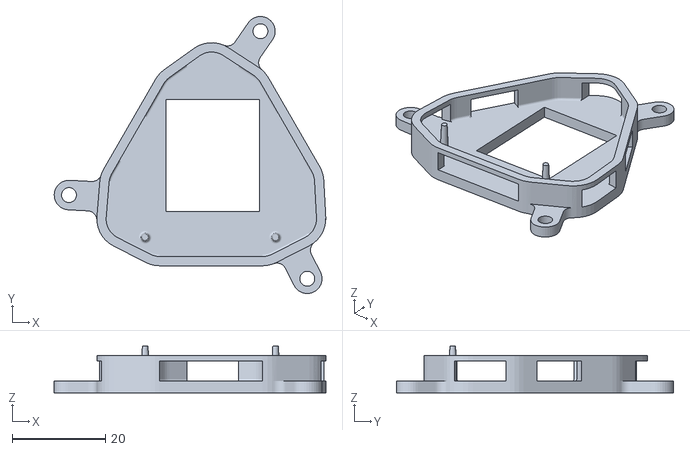
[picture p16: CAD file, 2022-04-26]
Mechanical + Electrical Files/Salamander Assembly/STL/Mainboard Shell Bottom.STL
58.3 x 59.5 x 10.0

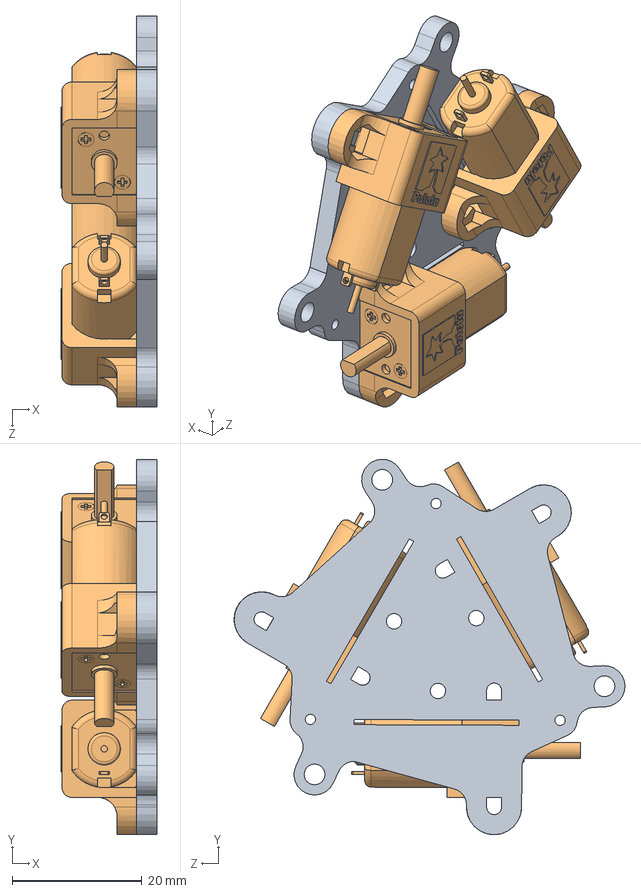
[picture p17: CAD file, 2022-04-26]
Mechanical + Electrical Files/Salamander Assembly/Final Version/Expansion Motor Mount.SLDASM
14.9 x 57.9 x 60.3 mm
motor_mounting_plate_v2
micro-metal-gearmotor-extended-with-1086-bracket x 3

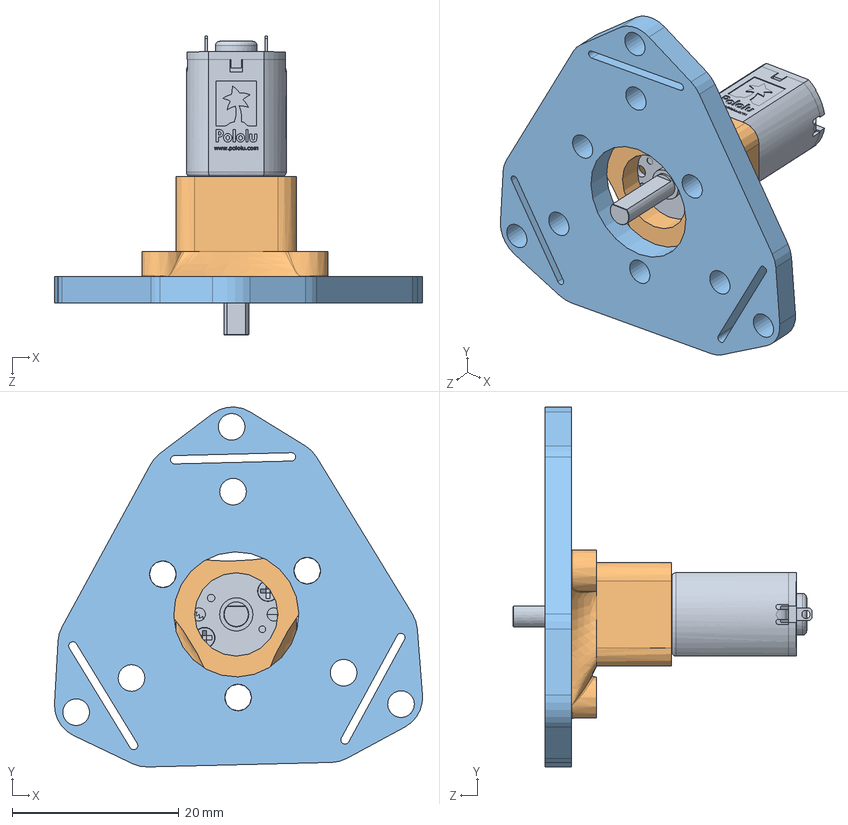
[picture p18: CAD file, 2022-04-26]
Mechanical + Electrical Files/Salamander Assembly/Alternative Version/Motor Flange.SLDASM
44.1 x 43.2 x 35.8 mm
micro-metal-gearmotor
Motor Flange
Top Acrylic Base

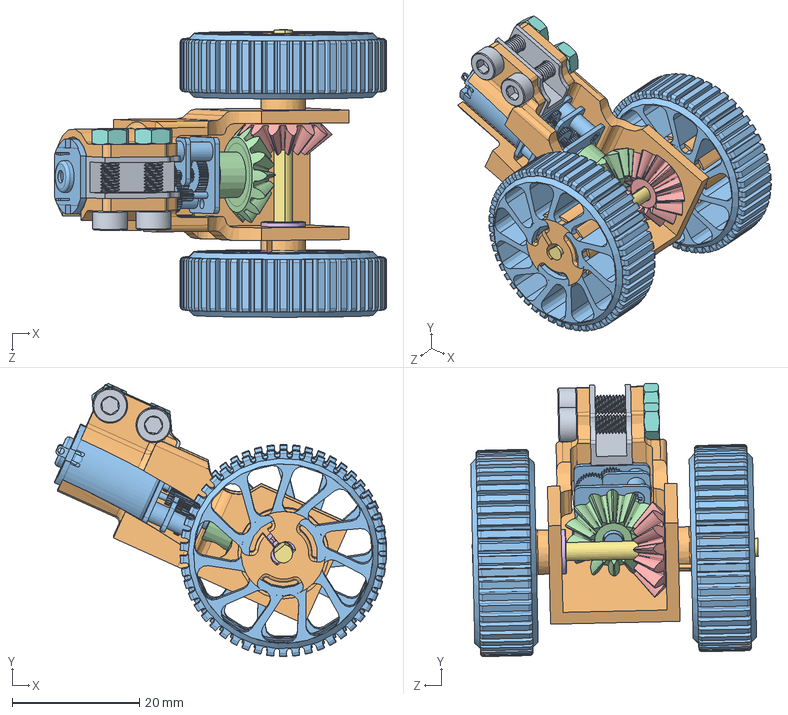
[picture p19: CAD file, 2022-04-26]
Mechanical + Electrical Files/Salamander Assembly/Final Version/Motor Housing 1.SLDASM
52.3 x 43.0 x 45.3 mm
Motor Base2
Motor Mount
micro-metal-gearmotor
With_convex-Metric - Straight miter gear 1M14T 20PA 5FW
Metric - Straight miter gear 1M14T 20PA 5FW ---14O10H8MD2N
57155K427_Stainless Steel Ball Bearing x 2
Dshaftd3l40
90592A085_STEEL HEX NUT x 2
91290A115_Black-Oxide Alloy Steel Socket Head Screw x 2
Outer Wheel v3 x 2
COmpression Wheel v5 x 2

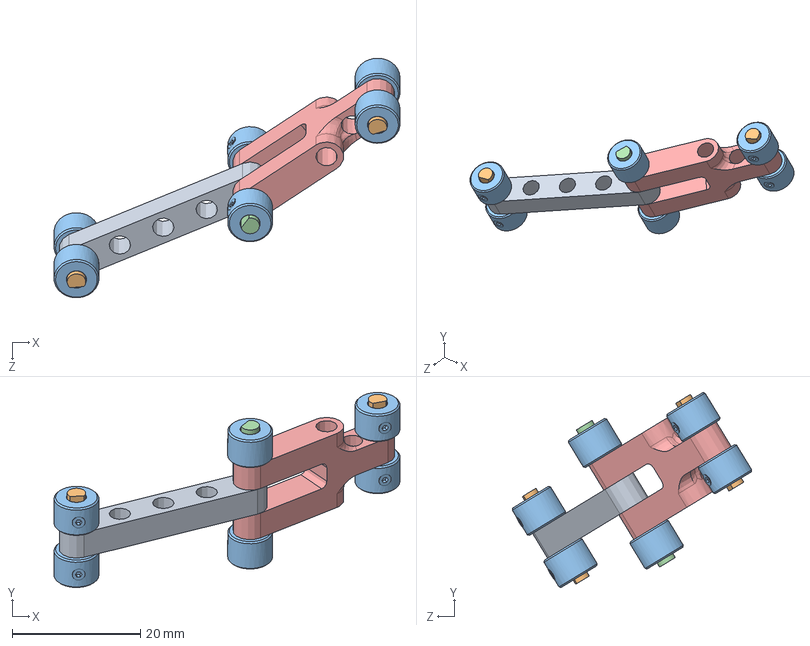
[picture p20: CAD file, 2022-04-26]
Mechanical + Electrical Files/Salamander Assembly/Alternative Version/Link Assembly.SLDASM
53.9 x 30.4 x 37.3 mm
Base Link
Aluminum D Shaft x 2
6056N11_Carbon Steel Set Screw Collar x 6
Link D Shaft
Upper Link

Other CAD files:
Mechanical + Electrical Files/Salamander Assembly/STL/Mainboard Shell Top.STL
Mechanical + Electrical Files/Salamander Assembly/Alternative Version/Top Wheel Housing.SLDASM
Mechanical + Electrical Files/Salamander Assembly/Final Version/Mainboard Shell Bottom.SLDPRT
Mechanical + Electrical Files/Salamander Assembly/Final Version/Motor Flange.SLDASM
Mechanical + Electrical Files/Altium/Version 1/Pololu Schematic.DXF
Mechanical + Electrical Files/Altium/Version 1/tinypico-hardware-master/tinypico-hardware-master/3D Files/TinyPICO Nano.stl
Mechanical + Electrical Files/Altium/Version 1/ul_A3910EEETR-T/AltiumDesigner/2021-10-04_20-19-53/DFN-8_ALM.step
Mechanical + Electrical Files/Altium/Version 1/ul_INA2180A1IDGKR/AltiumDesigner/2021-10-05_00-30-15/DGK8_TEX.step
Mechanical + Electrical Files/Altium/Version 1/ul_NCV1117ST50T3G/AltiumDesigner/2021-10-06_13-45-23/SOT223-3_ONS.step
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

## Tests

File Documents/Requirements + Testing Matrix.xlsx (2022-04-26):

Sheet: Long Term Full Robot TestsDemon
Requirement/Spec | Test Case Description | Demo or Test? | Testing/Demonstration Apparatus | Means of data collection | Expected Trials | Testing Faults | Notes | Testing Complete?
Robot must be able to travel in a straight line | Place robot on horizontal, flat surface, home robot, and drive straight | Test | flat surface | motion capture or slow-motion video | 5 | 1) homing robot is necessary to produce good results, surface could alter results | 1) Motion capture could be useful here 2) Use multiple surfaces
Robot maximum speed must be __ m/s | Utilize multiple flat surfaces with varying coefficients of friction (tile, cardboard, acrylic sheet, carpet) and propel the robot forward for a straight-line distance of 2 feet. Record the time it takes for the robot to travel across the surface for several trials, and record the average linear speed | Test | multiple surfaces (acrylic, metal, carpet) | motion capture or slow-motion video | 3 trials per surface | 1) homing robot is necessary to produce good results, surface could alter results | 1) Using a homing procedure using the current sensors on the SAMI boards and then extending to a desired length can ensure that the robot is straight when performing the test.
Robot must be able to traverse inclines | Use a smooth surface and gradually increase incline until robot is no longer able to climb | Test | various surfaces - we can vary incline and measure performance on each | measurement tools- protractor | N/A | this is surface dependant- so determining the surface(s) to use is a good question | 1) Potential surfaces include: acrylic, carpet, tile, aluminum
Robot minimum turning radius must be __ mm. | Run motors to bend body as much as possible and process results | Test | N/A | Motion capture or imaging we can analyze | ? | Will be dependent on robot length, different lengths will produce different results - can find the absolute minimal radius and record that result
Robot must be able to tow a payload | Suspend robot in vertical pipe and hang weights from it to determine maximum vertical payload prior to slip Move robot through vertical pipe going up and down with payload attached to rear wheels to see how payload affects motion | Test | clear pipe | Newton scale or Qualitative | ? | this is also surface dependant- could depend on things like battery depletion as well as pipe size. | May also want to test other conditions besides just vertical
Robot can travel through various horizontal pipe inner diameters | Send robot through 2' section of straight pipe horizontally | Demonstration | clear pipe in one diameter, opaque pipe in others | Qualitative | ? | For larger diameters, robot doesn't need to cling to edges of the pipe - it can just drive with 1-2 wheels in contact | (Current Design w/ 28.6mm diameter wheels and link mechanism: Min Diameter: 3.6", Max Diameter: 5.23") (Alternative Design w/ 28.6mm diameter wheels and camslot mechanism: Min Diameter: 4.38", Max Diameter: 5.16")
Robot can travel through various vertical pipe inner diameters | Send robot through 2' section of straight pipe vertically | Demonstration | clear pipe in one diameter, opaque pipe in others | Qualitative | ? | Coefficient of friction within pipe might not be enough and robot may begin to slip when it cannot apply enough force to the sides of the pipe
Robot can travel through 90 degree bends of various sizing | Send robot through section of straight pipe and travel through a 90 degree elbow to another section of straight pipe | Demonstration | clear pipe in one diameter, opaque straight pipe in others clear? or opaque 90 degree elbow | Qualitative | ? | Depends on robot length - at longer lengths the robot may naturally go through the elbow but at shorter lengths we may need to manipulate the direction manually | 1) Can test going through an elbow horizontally and vertically
Robot must be able to travel through expansions & contractions | Put robot into straight pipe and connect expander/reducer at the end. Once the robot reaches the fitting, send a command over WiFi/tether to make the robot reduce/expand to the corresponding diameter | Demonstration | clear pipe in one diameter, opaque expander/reducer in corresponding diameter |  | 3 within the contained environment and varying pipe diameters | There are reducers that are gradually reducing with a taper and ones that reduce/expand instantly - might be easier to use the instant fittings | 1) Set up an environment with a straight pipe leading to an expansion, followed by a straight pipe leading to a reducer. Change the robot's size using PID to the correct diameter, and then propel the robot forward.

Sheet: Short Term PCB Tests
Requirement/Spec | Test Case Description | Testing/Demonstration Materials | Testing Complete?
Mainboard should be able to communicate with motor driver using I2C | Mainboard should request data via I2C, the mainboard perform a calculation upon request and then return data to the mainboard | - SAMI PCB (as slave) - CLARA Mainboard (as master) - Arduino IDE | Yes
Serial Data Passthrough | SAMI Board should be able to return data via the Serial Monitor and UART | -SAMI PCB (as transmitter) -CLARA Mainboard -Arduino Uno Circuit (as receiver) -Arduino IDE | Yes
WiFi control | Mainboard should react to WiFi commands via an external TinyPICO | -External TinyPICO controller as transmitter -CLARA Mainboard as receiver -Arduino Uno Circuit -SAMI PCB -Arduino IDE | Yes
Motor must be able to move forward and reverse | Command motor driver on SAMI boards to send the motor forward for 5 seconds, and then reverse for 5 seconds. Continue the cycle until power is removed. | -SAMI PCB -MD9927 motor driver -ATMEGA328 Microcontroller -AVR ISP/Arduino Uno Circuit -Arduino IDE | Yes
Motor must be able to change speed | Send PWM signal at varying duty cycles to change the speed of the motor via Arduino IDE | -SAMI PCB -MD9927 motor driver -ATMEGA328 Microcontroller -AVR ISP/Arduino Uno Circuit -Arduino IDE | Yes
Current sensor should be able to sense current going into motor driver | Read output of current sensor through the ADC at no load, expected load, and stall configurations | -SAMI PCB -Current Sensor -Motor -ATMEGA328 Microcontroller -AVR ISP/Arduino Uno Circuit -Arduino IDE | Yes
Hall Effect Latches should read changes in the motors position | Set up interrupts on hall effect triggers to count a variable and see if they are triggered when 1) manually rotating an encoder wheel 2) running the motor. Performance will be evaluated by commanding the motor to spin one rotation and seeing the differences between the expected result and actual result | -SAMI PCB -2x Honeywell Hall-Effect Latch Sensors -1x Encoder Wheel -1x N20 Motor -ATMEGA328 Microcontroller -AVR ISP/Arduino Uno Circuit -Arduino IDE | Yes
Motor should be accurate in reaching desired positions | Create PID controller to control motor speed and use position as error | -Complete/Assembled SAMI PCB -AVR ISP/Arduino Uno Circuit -Arduino IDE | Yes
Connect multiple motors to Mainboard and command an individual motor through its unique address to complete PID control | -Create I2C interface, address components, and command a singular I2C address from the mainboard to perform the PID test | -2+ Complete/Assembled SAMI PCB -Complete/Assembled Mainboard -AVR ISP/Arduino Uno Circuit -Arduino IDE | Yes
Command Mainboard to perform PID test using WiFi | Program TinyPICO to receive commands via an external TinyPICO through ESP-NOW and perform a PID test | -1x Complete/Assembled SAMI PCB -Complete/Assembled Mainboard -2x TinyPICO -AVR ISP/Arduino Uno Circuit -Arduino IDE | Yes

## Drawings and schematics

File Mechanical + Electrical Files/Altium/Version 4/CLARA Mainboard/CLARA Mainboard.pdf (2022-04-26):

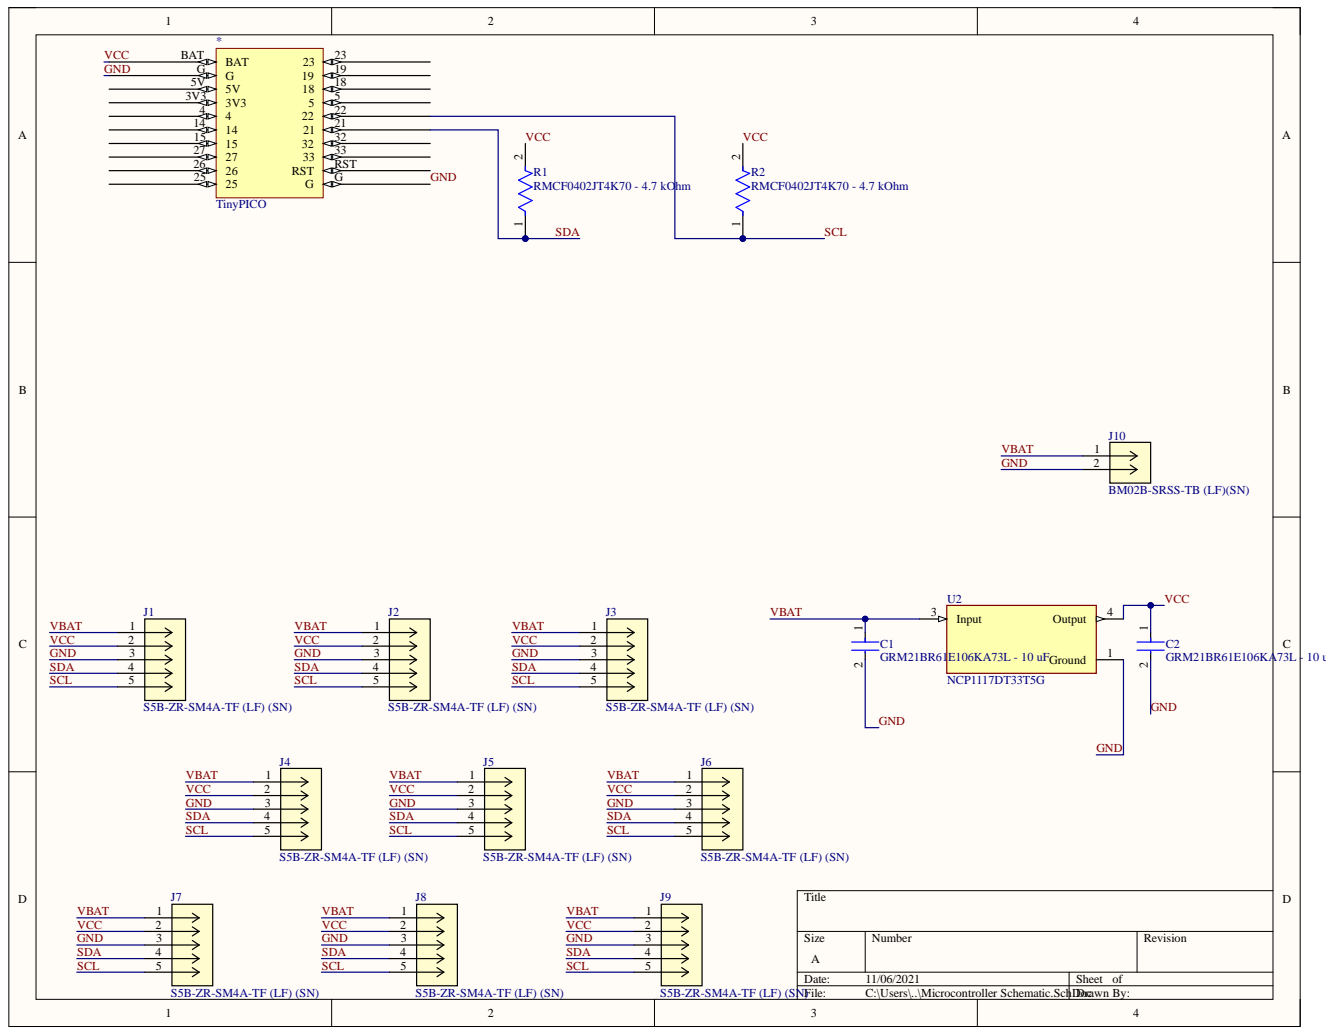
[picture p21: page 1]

GND

RMCF0402JT4K70 - 4.7 kOhm

BM02B-SRSS-TB (LF)(SN)

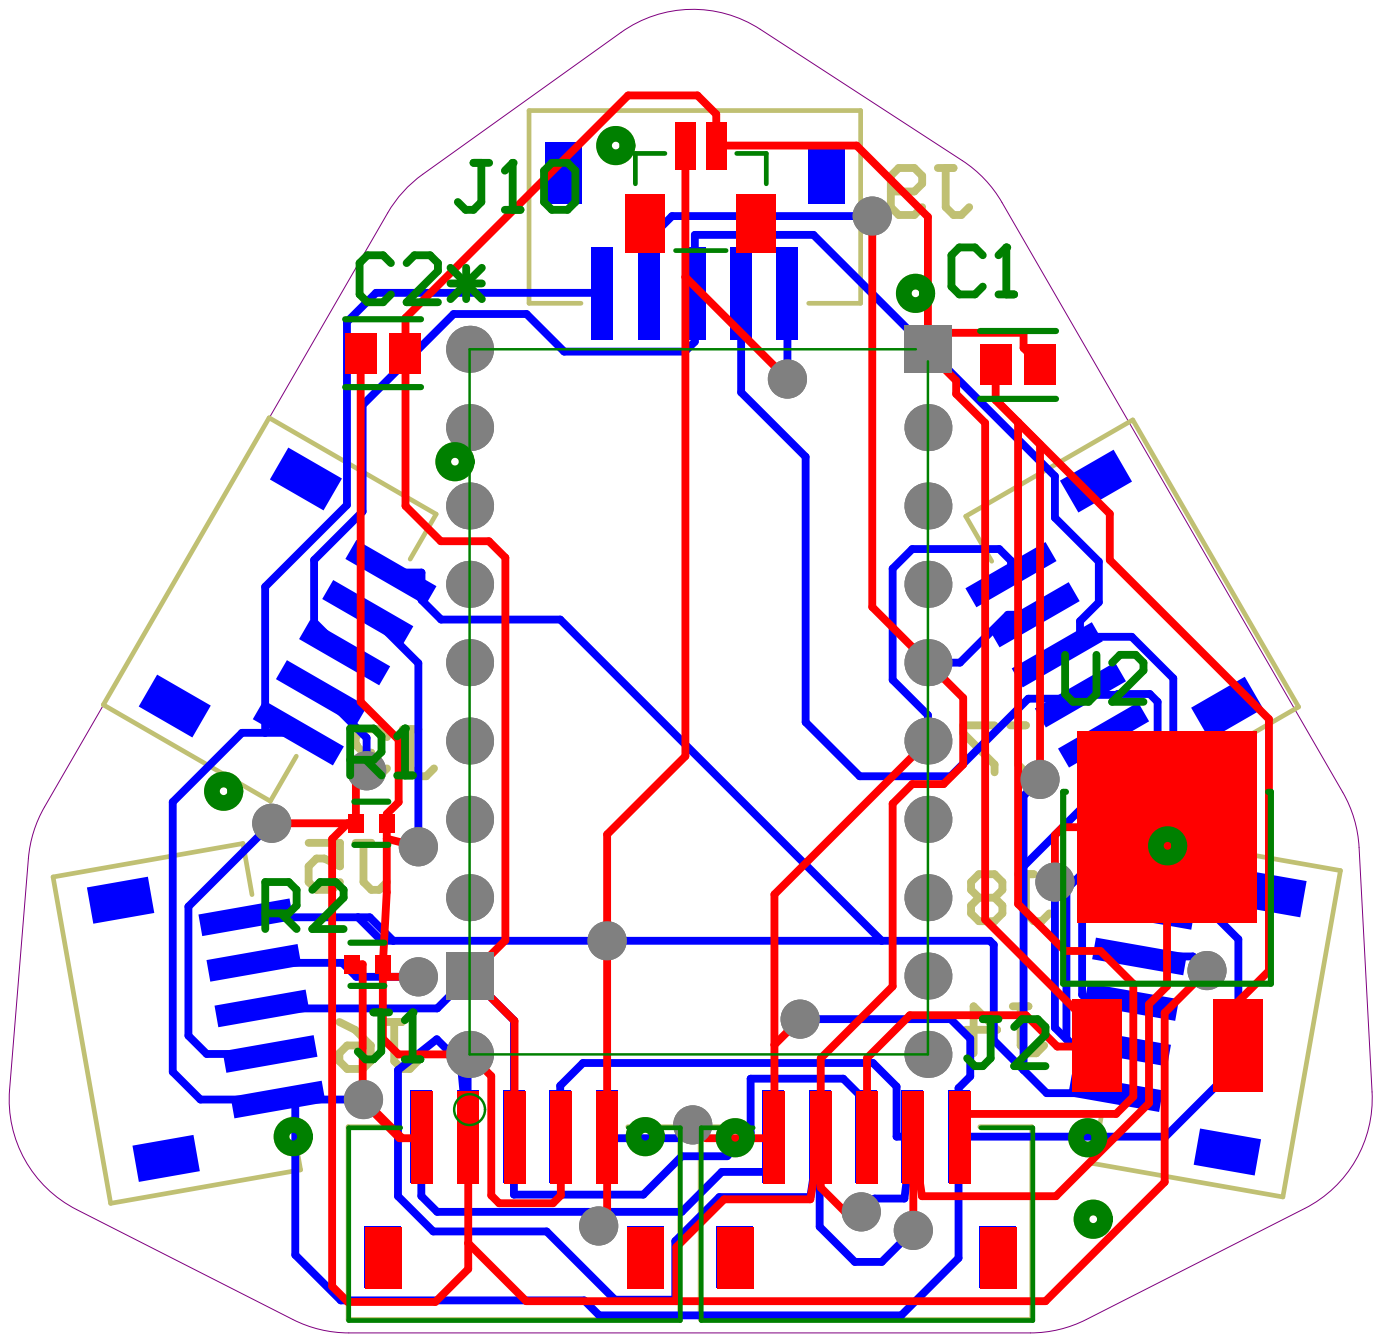
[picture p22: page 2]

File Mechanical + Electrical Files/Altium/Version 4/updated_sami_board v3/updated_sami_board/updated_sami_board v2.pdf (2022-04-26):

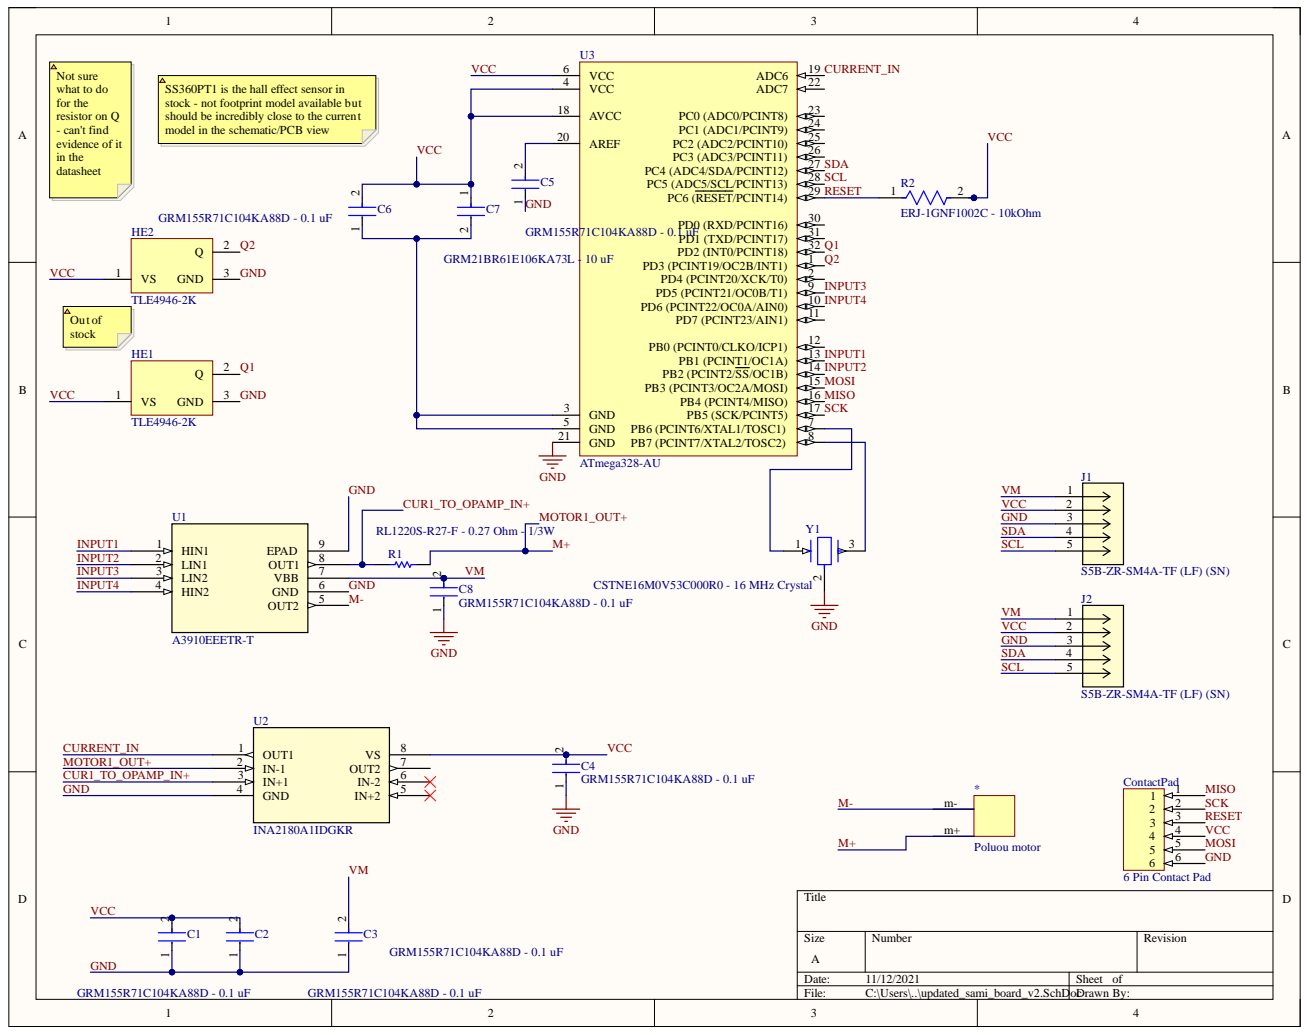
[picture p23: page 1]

SS360PT1 is the hall effect sensor in
stock - not footprint model available but
should be incredibly close to the current
model in the schematic/PCB view

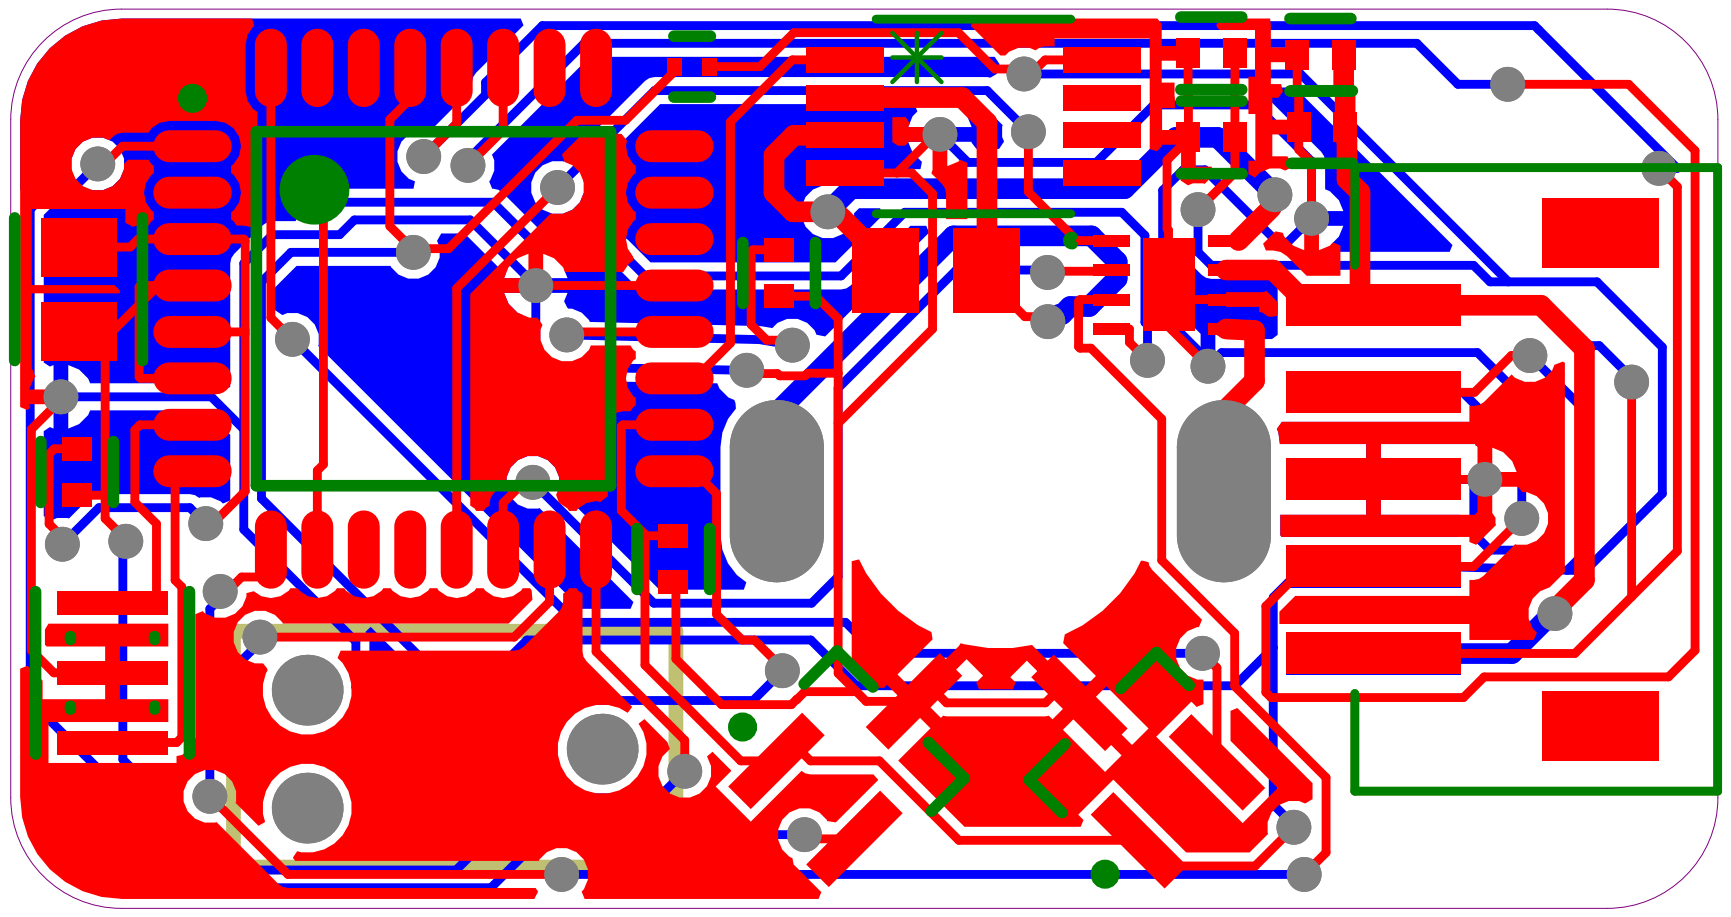
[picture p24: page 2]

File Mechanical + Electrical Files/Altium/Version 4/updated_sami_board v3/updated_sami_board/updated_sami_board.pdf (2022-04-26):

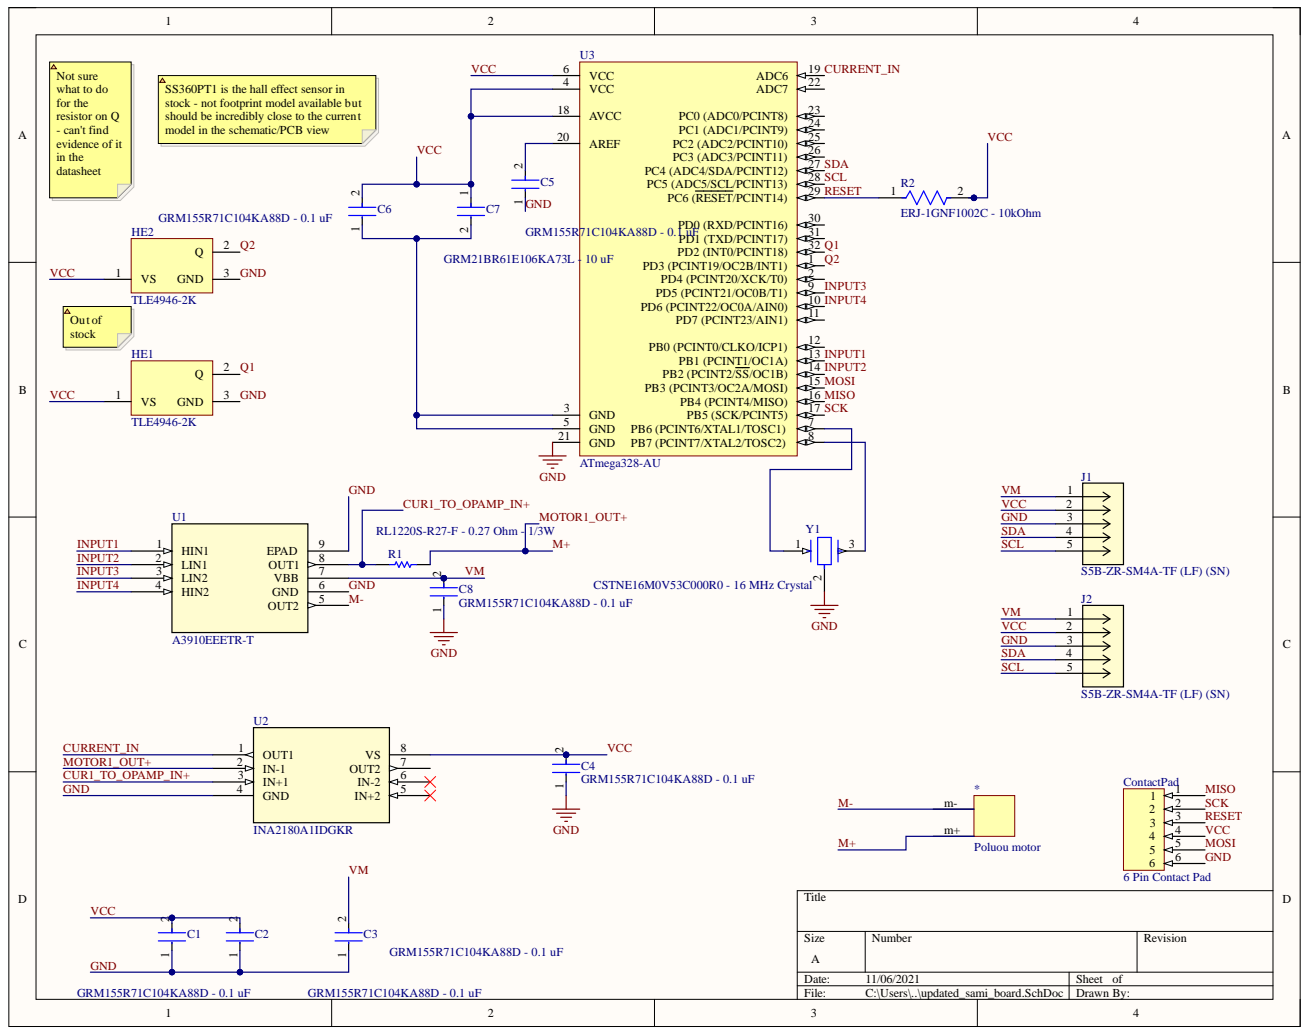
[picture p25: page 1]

SS360PT1 is the hall effect sensor in
stock - not footprint model available but
should be incredibly close to the current
model in the schematic/PCB view

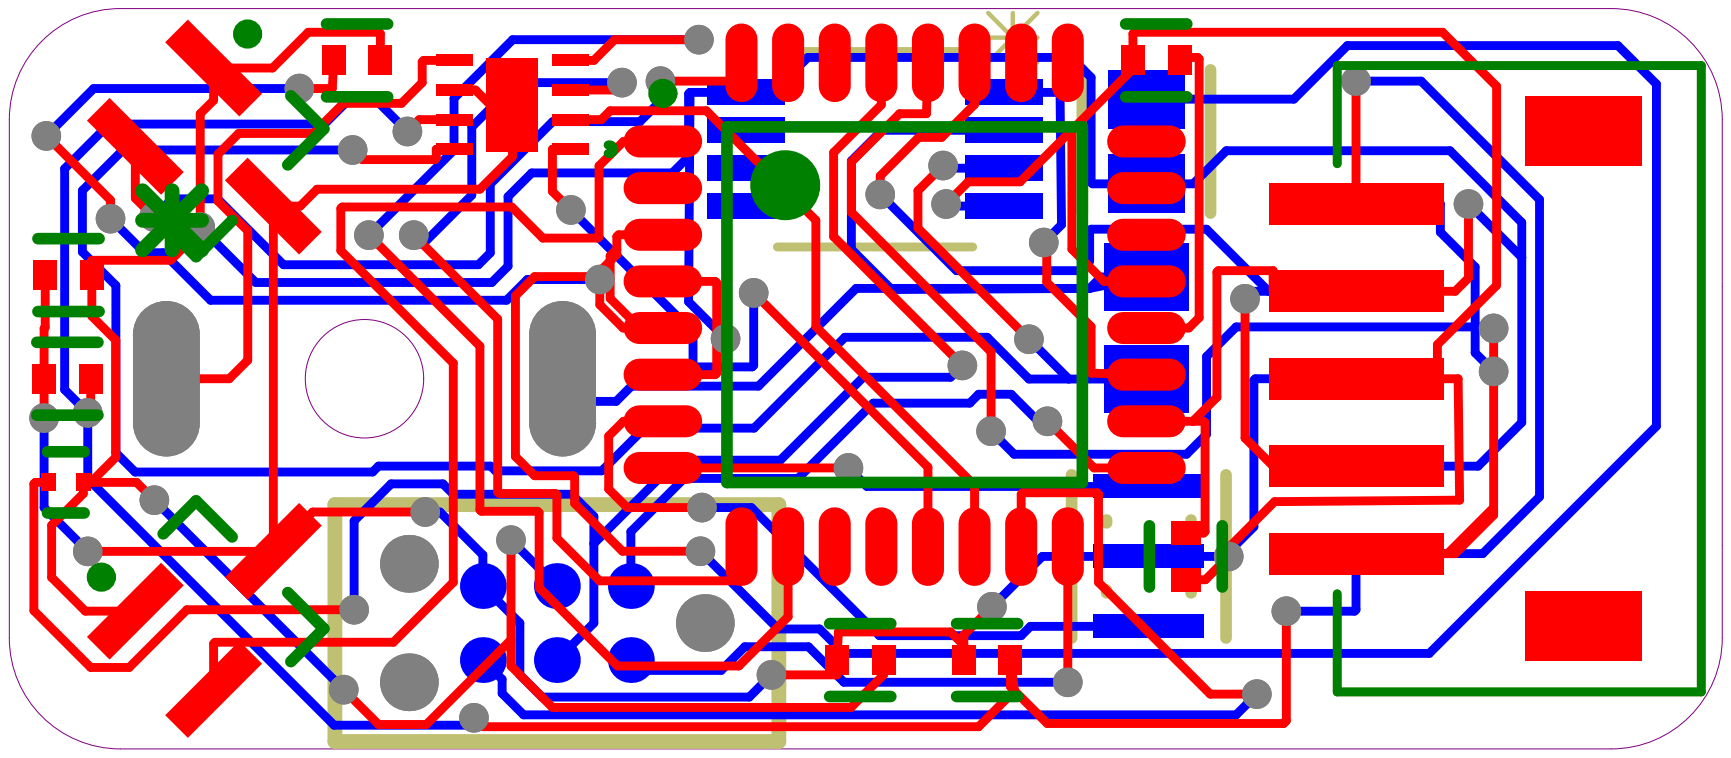
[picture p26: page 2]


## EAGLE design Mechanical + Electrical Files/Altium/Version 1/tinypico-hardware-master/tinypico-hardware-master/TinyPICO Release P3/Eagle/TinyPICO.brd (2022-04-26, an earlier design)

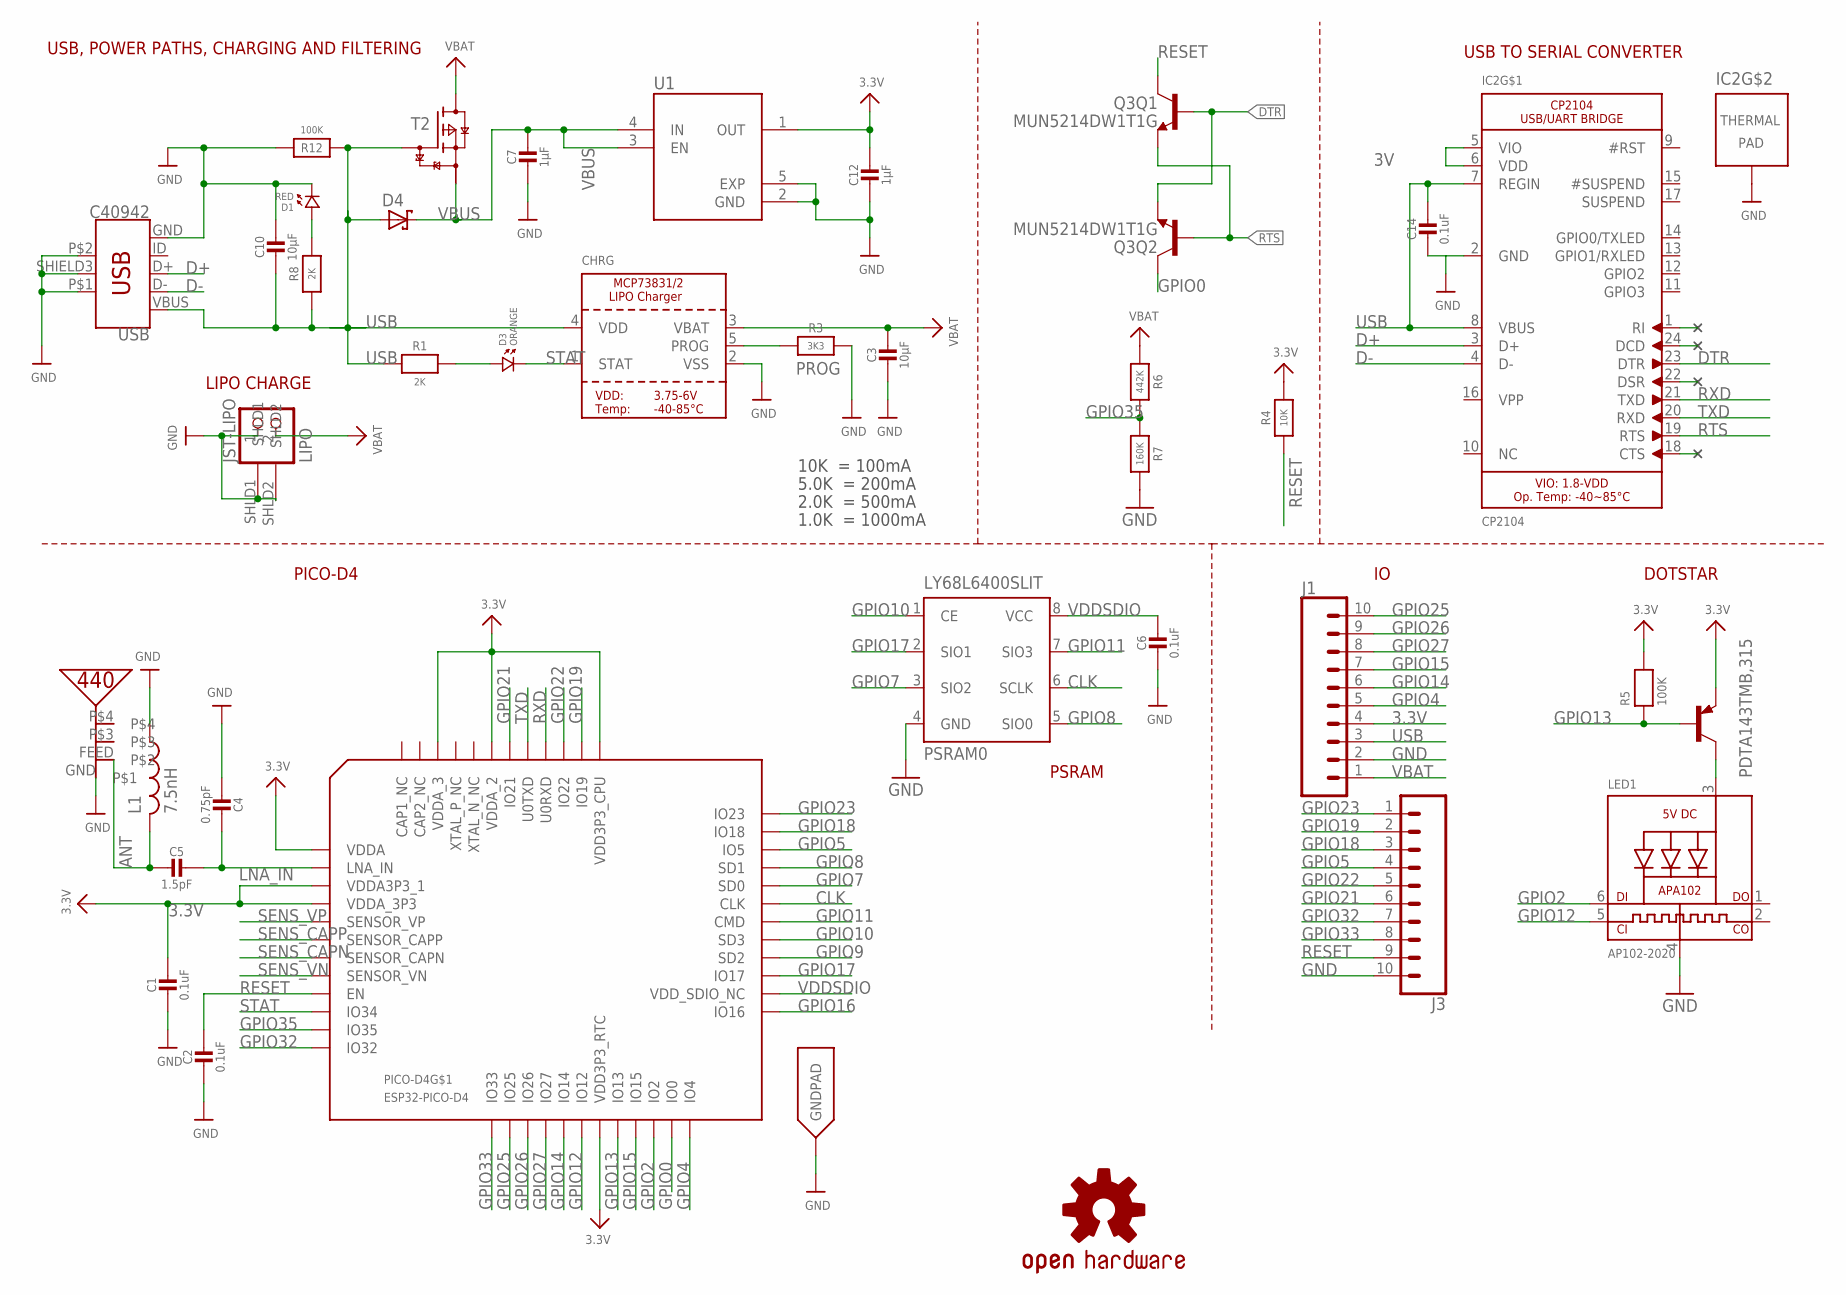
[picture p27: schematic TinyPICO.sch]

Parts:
C1, C2, C6, C14: 0.1uF; _0402MP
C3, C10: 10µF; _0603MP
C4: 0.75pF; _0402MP
C5: 1.5pF; _0402MP
C7, C12: 1µF; _0402MP
CHRG: TP4065-4.2V-SOT25-R; SOT23-5
D1: RED; 0402.LED
D3: ORANGE; 0402.LED
D4: BAT60J; SOD323_ST
IC2: CP2104; MICROBUILDER_QFN24_4MM_SMSC
J1, J3: TINYPICO_HEADER_10NO_SILK_PTH_FEMALE; 1X10_NO_SILK
JST-LIPO: LIPO; JSTPH2
L1: 7.5nH; RESC0402_N
LED1: AP102-2020; MICROBUILDER_APA102_2020
LOGO1: OSHW-LOGOS; OSHW-LOGO-S
LY68L6400SLIT: PSRAM0; SOP8
PDTA143TMB,315: TINYPICO-PNPAMB; SOT883(B)
PICO-D4: ESP32-PICO-D4; PICO-D4-QFN48
Q3: MUN5214DW1T1G; DUAL_NPN_SC70-6
R1, R8: 2K; _0402MP
R3: 3K3; _0402MP
R4: 10K; _0402MP
R5, R12: 100K; _0402MP
R6: 442K; _0402MP
R7: 160K; _0402MP
T2: TINYPICO-P-FETKMB; SOT883(B)
U1: NCP170AMX300TCG; VREG_NCP170AMX300TCG
U$8: PRO-OB-440
USB: C40942; USB-B-MICRO-SMD

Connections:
3.3V: C1.1, C12.1, J1.4, PDTA143TMB,315.2 (E), PICO-D4.1 (VDDA), PICO-D4.3 (VDDA3P3_1), PICO-D4.4 (VDDA_3P3), PICO-D4.19 (VDD3P3_RTC), PICO-D4.37 (VDD3P3_CPU), PICO-D4.43 (VDDA_2), PICO-D4.46 (VDDA_3), R4.2, R5.2, U1.1 (OUT)
3V: IC2.5 (VIO), IC2.6 (VDD)
ANT: C5.2, L1.2, U$8.FEED
CLK: LY68L6400SLIT.6 (SCLK), PICO-D4.31 (CLK)
D+: IC2.3 (D+), USB.D+
D-: IC2.4 (D-), USB.D-
DTR: IC2.23 (DTR), Q3.1 (E), Q3.5 (B)
GND: C1.2, C2.2, C3.2, C4.2, C6.2, C7.2, C10.1, C12.2, C14.2, CHRG.2 (VSS), D1.P$2 (2), IC2.2 (GND), IC2.THERM (TP), J1.2, J3.10, JST-LIPO.1, JST-LIPO.SHLD1, JST-LIPO.SHLD2, L1.1, LED1.4 (GND), LY68L6400SLIT.4 (GND), PICO-D4.EXP (GNDPAD), R3.2, R7.2, R12.2, U1.2 (GND), U1.5 (EXP), U$8.GND, USB.GND, USB.P$1 (SHIELD1), USB.P$2 (SHIELD2), USB.SHIELD3 (SHIELD)
GPIO0: PICO-D4.23 (IO0), Q3.6 (C)
GPIO2: LED1.6 (DI), PICO-D4.22 (IO2)
GPIO4: J1.5, PICO-D4.24 (IO4)
GPIO5: J3.4, PICO-D4.34 (IO5)
GPIO7: LY68L6400SLIT.3 (SIO2), PICO-D4.32 (SD0)
GPIO8: LY68L6400SLIT.5 (SIO0), PICO-D4.33 (SD1)
GPIO9: PICO-D4.28 (SD2)
GPIO10: LY68L6400SLIT.1 (CE), PICO-D4.29 (SD3)
GPIO11: LY68L6400SLIT.7 (SIO3), PICO-D4.30 (CMD)
GPIO12: LED1.5 (CKI), PICO-D4.18 (IO12)
GPIO13: PDTA143TMB,315.1 (B), PICO-D4.20 (IO13), R5.1
GPIO14: J1.6, PICO-D4.17 (IO14)
GPIO15: J1.7, PICO-D4.21 (IO15)
GPIO16: PICO-D4.25 (IO16)
GPIO17: LY68L6400SLIT.2 (SIO1), PICO-D4.27 (IO17)
GPIO18: J3.3, PICO-D4.35 (IO18)
GPIO19: J3.2, PICO-D4.38 (IO19)
GPIO21: J3.6, PICO-D4.42 (IO21)
GPIO22: J3.5, PICO-D4.39 (IO22)
GPIO23: J3.1, PICO-D4.36 (IO23)
GPIO25: J1.10, PICO-D4.14 (IO25)
GPIO26: J1.9, PICO-D4.15 (IO26)
GPIO27: J1.8, PICO-D4.16 (IO27)
GPIO32: J3.7, PICO-D4.12 (IO32)
GPIO33: J3.8, PICO-D4.13 (IO33)
GPIO35: PICO-D4.11 (IO35), R6.2, R7.1
LNA_IN: C4.1, C5.1, PICO-D4.2 (LNA_IN)
unnamed: D1.P$1 (1), R8.2
unnamed: D3.P$1 (1), R1.2
unnamed: LED1.3 (VDD), PDTA143TMB,315.3 (C)
PROG: CHRG.5 (PROG), R3.1
RESET: C2.1, J3.9, PICO-D4.9 (EN), Q3.3 (C), R4.1
RTS: IC2.19 (RTS), Q3.2 (B), Q3.4 (E)
RXD: IC2.21 (TXD), PICO-D4.40 (U0RXD)
SENS_CAPN: PICO-D4.7 (SENSOR_CAPN)
SENS_CAPP: PICO-D4.6 (SENSOR_CAPP)
SENS_VN: PICO-D4.8 (SENSOR_VN)
SENS_VP: PICO-D4.5 (SENSOR_VP)
STAT: CHRG.1 (STAT), D3.P$2 (2), PICO-D4.10 (IO34)
TXD: IC2.20 (RXD), PICO-D4.41 (U0TXD)
USB: C10.2, C14.1, CHRG.4 (VDD), D4.A, IC2.7 (REGIN), IC2.8 (VBUS), J1.3, R1.1, R8.1, R12.1, T2.1 (G), USB.VBUS
VBAT: C3.1, CHRG.3 (VBAT), J1.1, JST-LIPO.2, R6.1, T2.3 (D)
VBUS: C7.1, D4.C, T2.2 (S), U1.3 (EN), U1.4 (IN)
VDDSDIO: C6.1, LY68L6400SLIT.8 (VCC), PICO-D4.26 (VDD_SDIO_NC)

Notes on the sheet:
USB, POWER PATHS, CHARGING AND FILTERING
LIPO CHARGE
USB TO SERIAL CONVERTER
PICO-D4
10K = 100mA
5.0K = 200mA
2.0K = 500mA
1.0K = 1000mA
PSRAM
DOTSTAR

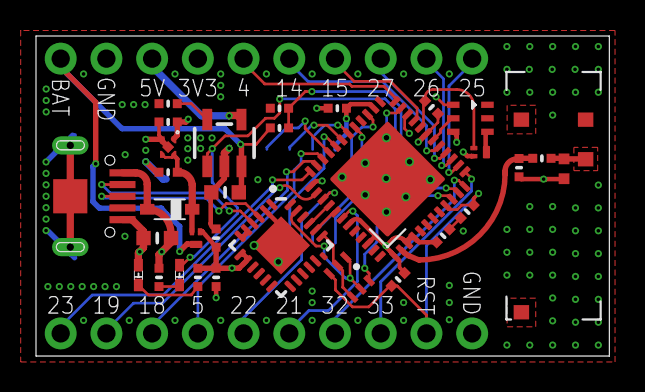
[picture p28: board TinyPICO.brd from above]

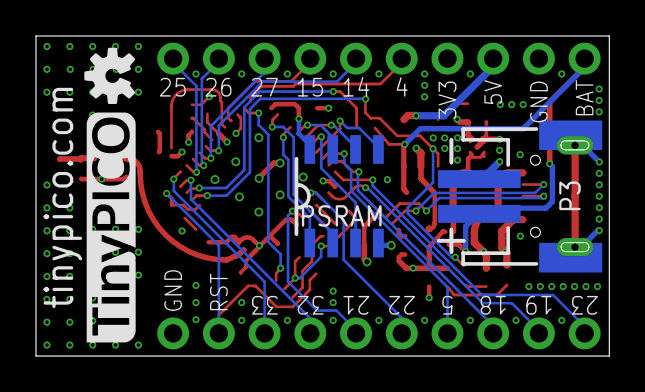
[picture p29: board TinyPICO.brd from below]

Board: 4 copper layers, 31.9 x 17.8 mm, 37 parts (3 on the bottom side), 46 nets.

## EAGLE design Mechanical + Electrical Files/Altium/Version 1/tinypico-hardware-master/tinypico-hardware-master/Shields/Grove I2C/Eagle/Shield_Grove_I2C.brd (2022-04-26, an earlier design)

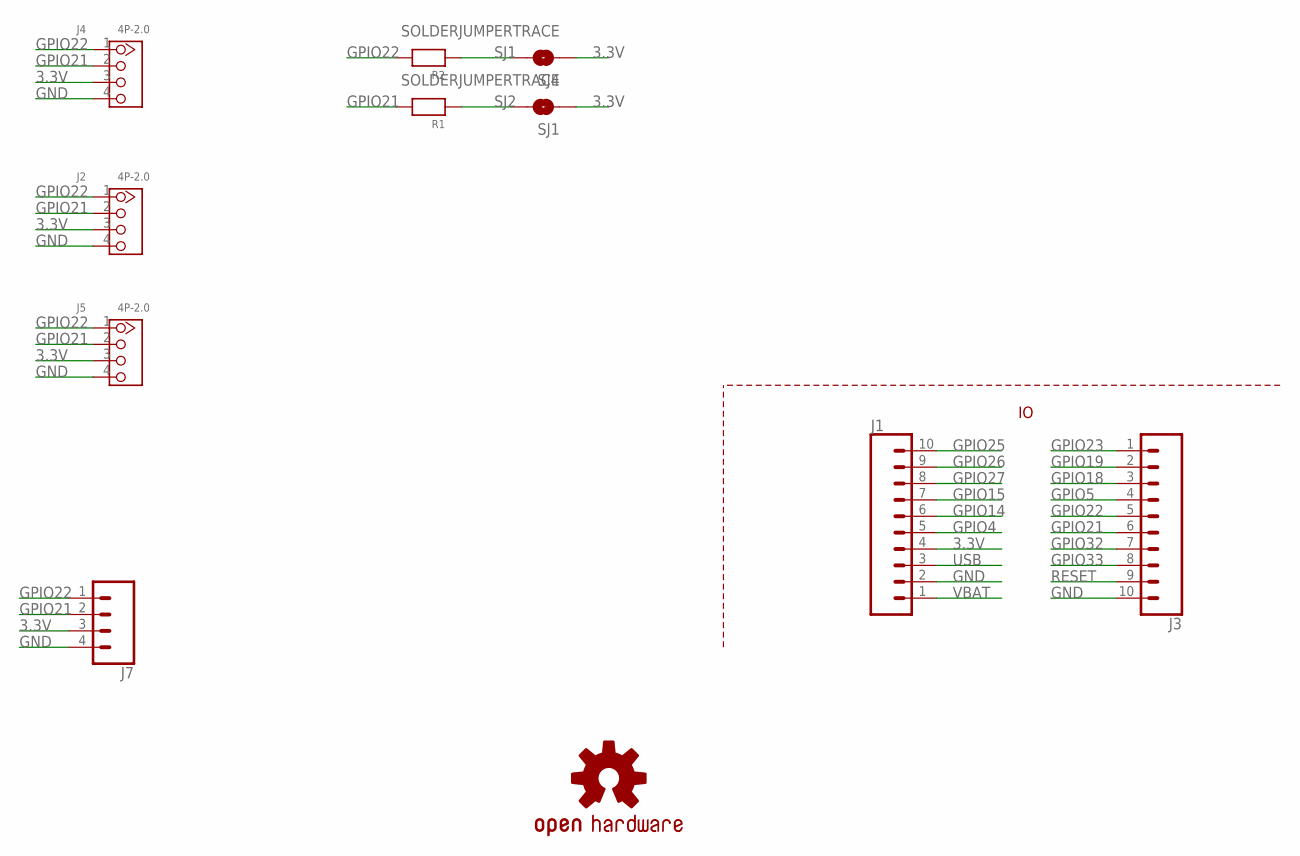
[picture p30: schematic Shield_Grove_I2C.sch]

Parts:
J1, J3: TINYPICO_HEADER_10NO_SILK_PTH_FEMALE; 1X10_NO_SILK
J2, J4, J5: 4P-2.0; HW4-2.0
J7: CONN_041X04_NO_SILK; 1X04_NO_SILK
LOGO1: OSHW-LOGOS; OSHW-LOGO-S
R1, R2: RESISTOR_0603MP; _0603MP
SJ1, SJ4: SOLDERJUMPERTRACE; SPARKFUN_SJ_2S-TRACE

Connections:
3.3V: J1.4, J2.3, J4.3, J5.3, J7.3, SJ1.1, SJ4.1
GND: J1.2, J2.4, J3.10, J4.4, J5.4, J7.4
GPIO4: J1.5
GPIO5: J3.4
GPIO14: J1.6
GPIO15: J1.7
GPIO18: J3.3
GPIO19: J3.2
GPIO21: J2.2, J3.6, J4.2, J5.2, J7.2, R1.2
GPIO22: J2.1, J3.5, J4.1, J5.1, J7.1, R2.2
GPIO23: J3.1
GPIO25: J1.10
GPIO26: J1.9
GPIO27: J1.8
GPIO32: J3.7
GPIO33: J3.8
RESET: J3.9
SJ1: R2.1, SJ4.2
SJ2: R1.1, SJ1.2
USB: J1.3
VBAT: J1.1

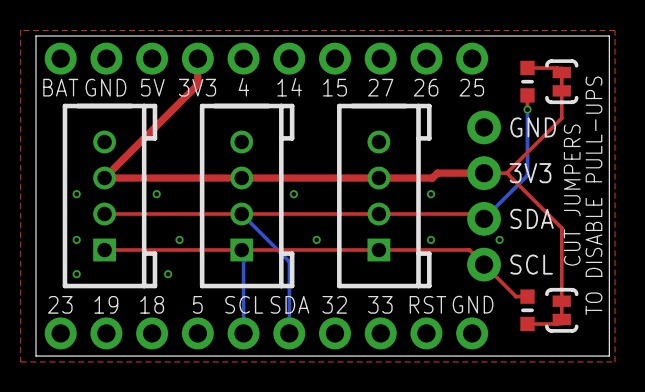
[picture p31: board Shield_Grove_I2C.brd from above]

Board: 2 copper layers, 31.9 x 17.8 mm, 11 parts (1 on the bottom side), 6 nets.

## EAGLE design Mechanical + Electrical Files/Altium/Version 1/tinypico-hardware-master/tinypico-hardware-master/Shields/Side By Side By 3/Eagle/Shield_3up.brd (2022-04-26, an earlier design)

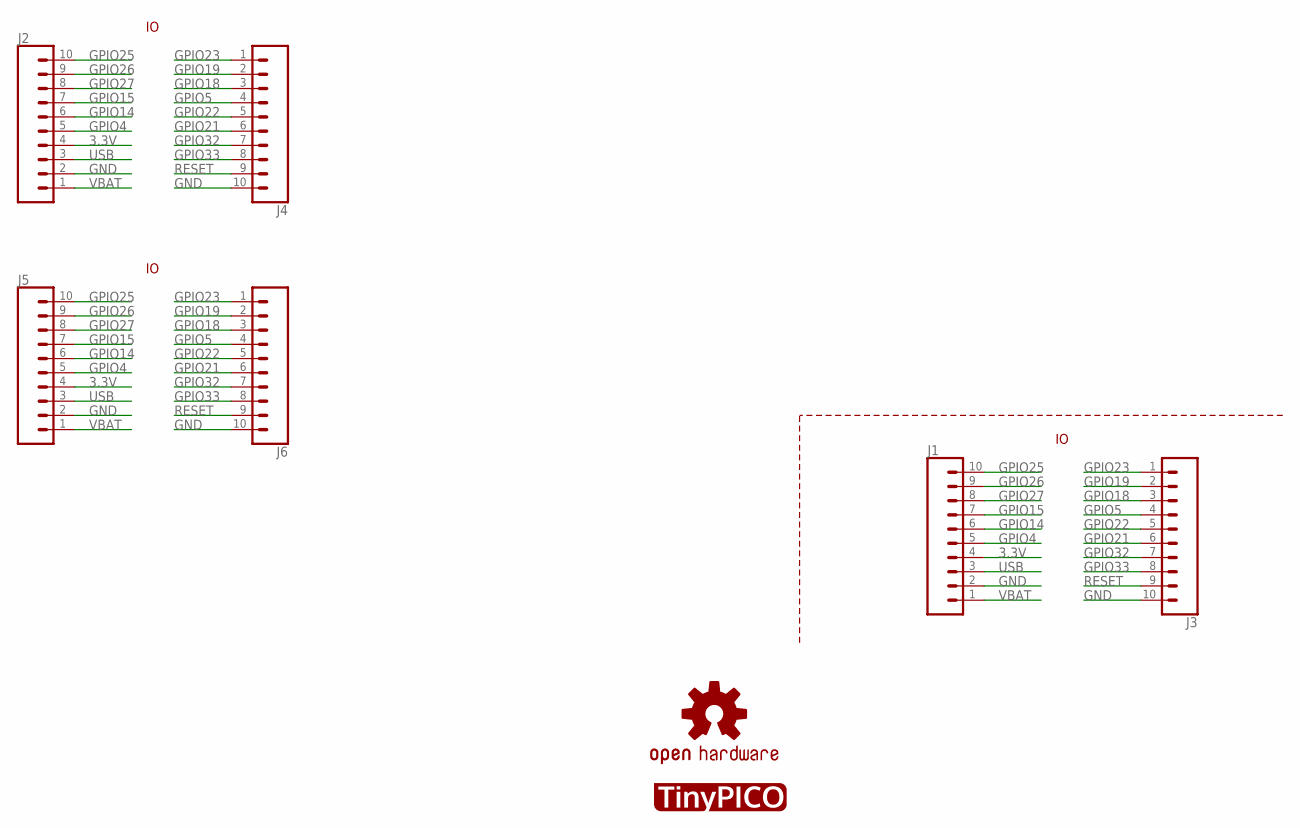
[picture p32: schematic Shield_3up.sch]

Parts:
J1, J2, J3, J4, J5, J6: TINYPICO_HEADER_10NO_SILK_PTH_FEMALE; 1X10_NO_SILK
LOGO1: OSHW-LOGOS; OSHW-LOGO-S
U$1: TP_LOGO

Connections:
3.3V: J1.4, J2.4, J5.4
GND: J1.2, J2.2, J3.10, J4.10, J5.2, J6.10
GPIO4: J1.5, J2.5, J5.5
GPIO5: J3.4, J4.4, J6.4
GPIO14: J1.6, J2.6, J5.6
GPIO15: J1.7, J2.7, J5.7
GPIO18: J3.3, J4.3, J6.3
GPIO19: J3.2, J4.2, J6.2
GPIO21: J3.6, J4.6, J6.6
GPIO22: J3.5, J4.5, J6.5
GPIO23: J3.1, J4.1, J6.1
GPIO25: J1.10, J2.10, J5.10
GPIO26: J1.9, J2.9, J5.9
GPIO27: J1.8, J2.8, J5.8
GPIO32: J3.7, J4.7, J6.7
GPIO33: J3.8, J4.8, J6.8
RESET: J3.9, J4.9, J6.9
USB: J1.3, J2.3, J5.3
VBAT: J1.1, J2.1, J5.1

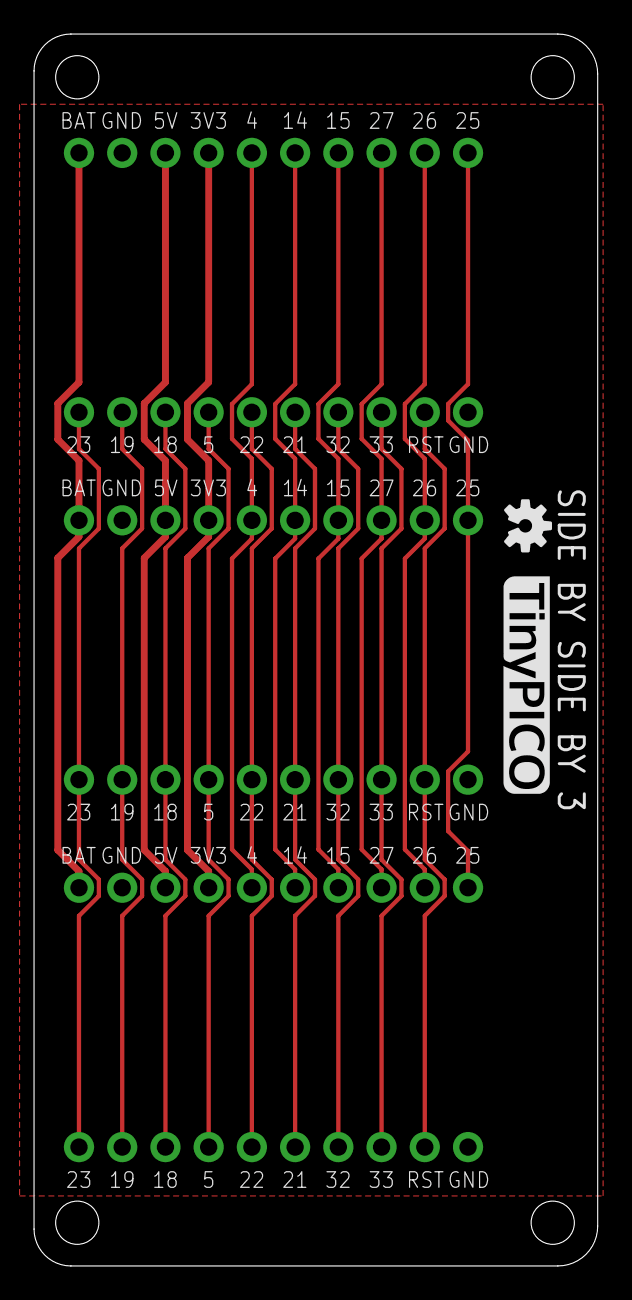
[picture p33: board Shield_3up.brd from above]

Board: 2 copper layers, 33.1 x 72.4 mm, 8 parts (1 on the bottom side), 19 nets.

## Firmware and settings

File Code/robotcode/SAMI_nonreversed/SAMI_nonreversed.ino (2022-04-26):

/**
   To be uploaded on motor driver module boards - Handle motor motion and control internally
*/

// NANO -> ATMEGA328-AU Board Pin Mapping
//  Nano dec port   ATMega328-AU            Nano dec port       ATMega328-AU
//  -------------   --------------------    -------------    -------------------
//  pin (12) D12 -> IC pin 16 (MISO)        pin (13) D13  -> IC pin 17 (SCK)
//  pin (11) D11 -> IC pin 15 (MOSI)        pin 3.3V
//  pin (10) D10 -> IC pin 14 (PB2)         pin AREF -> IC pin 20 (AREF)
//  pin ( 9) D09 -> IC pin 13 (PB1)         pin (14) PC0  -> IC pin 23 (PC0/ADC0)
//  pin ( 8) D08 -> IC pin 12 (PB0)         pin (15) PC1  -> IC pin 24 (PC1/ADC1)
//  pin ( 7) D07 -> IC pin 11 (PD7)         pin (16) PC2  -> IC pin 25 (PC2/ADC2)
//  pin ( 6) D06 -> IC pin 10 (PD6)         pin (17) PC3  -> IC pin 26 (PC3/ADC3)
//  pin ( 5) D05 -> IC pin 09 (PD5)         pin (18) PC4  -> IC pin 27 (PC4/ADC4)
//  pin ( 4) D04 -> IC pin 02 (PD4)         pin (19) PC5  -> IC pin 28 (PC5/ADC5)
//  pin ( 3) D03 -> IC pin 01 (PD3)         pin (??) ADC6 -> IC pin 19 (ADC6)
//  pin ( 2) D02 -> IC pin 32 (PD2/INT0)    pin (??) ADC7 -> IC pin 22 (ADC7)
//  pin (??) RST -> IC pin 29 (PC6/RESET)   pin (??) PC6  -> IC pin 29 (RESET/PC6)
//  pin (??) RXD -> IC pin 30 (RX/PD0)      pin GND
//  pin (??) TXD -> IC pin 31 (TX/PD1)      pin VIN
//  --- --- -> IC pin 08 (PB7/OSC2)    --- ---  -> IC pin 07 (PB8/OSC1)
//  --- --- -> IC pin 03/05/21 (GND)   --- ---  -> IC pin 04/06/18 (VCC/VCC/AVCC)

#include <Wire.h>
#include <math.h>


/**********************************************************************************************************************

                                                    VARIABLES + DEFINITIONS


 **********************************************************************************************************************/

/*******************************************
     PIN DEFINITIONS - Arduino Nano pins
 *****************************************/
#define NSLEEP 5
#define INPUT1 9
#define INPUT2 10
#define currentRead 17 //26
#define enc1 2 //32
#define enc2 3 //1 

/******************************************
                 VARIABLES
 *****************************************/
//Motor speed definitions
int slow = 100; //default slow speed
int fast = 500; //default fast speed
int fastSpeed = 255; //cabl75e motor speeds - this gets changed throughout the program
int slowRPM = 75;
int fastRPM = 25;

//Current Sensor variables
float stall_current = 0.00; // 0.25; //current value when motor is stalled
float motorCurrent = 0.00; //data variable representing motor current sent through I2C to mainboard
//bool motorstalled;
long lastTime = 0; //previous time current was checked
bool motorstalleddown, motorstalledup; //motor stalled variables

//Encoder variables
volatile int16_t count = 0; //current encoder count - sent through I2C to mainboard

//I2C Variables
byte address = 0x07; //the address of the board being flashed
char I2Cstatus = '0'; //I2C command sent from Mainboard
byte data[4]; //the data variable to be sent along I2C

//PID variables
float kp = 0.2; //proportional constant
int result = 0; //PID result placeholder variable
int lastcount = 0; //placeholder for previous count of encoder ticks
int motSpeed = 0; //motor speed, RPM
int countdiff = 0; //difference in encoder count from lastcount to current count
int calcSpeedPID = 0; //PID calculation result
const int Ngear = 298; //motor gear ratio
int currenterror = 0; //current motor speed error for PID
int targetSpeed = 0; //target speed in RPM
int cablelength = 0; //cable length in m



/**********************************************************************************************************************

                                                         SETUP + LOOP


 **********************************************************************************************************************/

void setup() {
  //set up I2C for the given address
  Wire.begin(address);

  // set up sensor pins
  pinMode(currentRead, INPUT);
  pinMode(enc1, INPUT);
  pinMode(enc2, INPUT);

  //attach interrupts on both encoders w/ isr callback functions for each of them - speeds up ISRs
  attachInterrupt(digitalPinToInterrupt(enc1), isr1, CHANGE);
  attachInterrupt(digitalPinToInterrupt(enc2), isr2, CHANGE);

  //set up I2C event channels
  Wire.onRequest(requestEvent); //upon receiving a request from the master, call requestEvent
  Wire.onReceive(msgEvent); //upon receiving a message the I2C device, call msgEvent

  digitalWrite(NSLEEP, HIGH); //  nSleep should be kept high for normal operation of the MD9927 motor driver

  //if the current address is one of the cable motors (4,5,6) - reduce maximum speed to 150 for more control
  if (address == 0x04 | address == 0x05 | address == 0x06 ) {
    fastSpeed = 150;
  }
}


void loop() {
  if ((millis() - lastTime) >= 10) { //calculate PID every 20ms

    //calculate current RPM and compute PID with it
    countdiff = count - lastcount; //difference in encoder count
    lastcount = count;

    //calculate motor speed in RPM
    motSpeed = abs(countdiff * 1.67); //((1000*60)/(12*20*Ngear))) i dont know why it hates actual math.u.. ;
    currenterror = targetSpeed - motSpeed; //calculate current error from our target speed
    calcSpeedPID = calcPID(currenterror); //calculate PID
    //cablelength = calcCablelen(count)*10;

    lastTime = millis(); //update timer
  }

  //check the current sensor
  readCurrent();

  //switch statement given i2c input command from command line or controller
  switch (I2Cstatus) {
    default: //no message- status defaults to zero
      break;
    case 0: //motor stop
      brake();
      break;
    case 1: //lead screw up speed
      reverse(250);
      break;
    case 2: //lead screw down speed
      forward(250);
      break;
    case 3: //if motor is stalled, brake
      if (motorstalleddown) {
        brake();
        //delay(200);
        I2Cstatus = 0;

      } else {
        forward(150);
      }
      break;
    case 4: //if motor is stalled, brake
      if (motorstalledup) {
        brake();
        //delay(200);
        I2Cstatus = 0;

      } else {
        reverse(150);
      }
      break;
    case 9: //cable motor
      reverse(200);
      break;
    case 8: //cable motor
      forward(200);
      break;
    case 11:
      targetSpeed = slowRPM;
      if (address == 0x01) {
        reverse(calcSpeedPID);
      } else {
        reverse(calcSpeedPID);
      }
      break;
    case 10:
      targetSpeed = slowRPM;
      if (address == 0x01) {
        forward(calcSpeedPID);
      } else {
        forward(calcSpeedPID);
      }
      break;

    case 12: //cable up speed
      targetSpeed = slowRPM;
      forward(calcSpeedPID);
      break;
    case 13: //cable down speed
      targetSpeed = slowRPM;
      reverse(calcSpeedPID);
      break;
    case 14: //attempt piD position
      long pidtarget = 10000;
      if (pidposition(pidtarget)) {

        brake;
        I2Cstatus = 0;
      }
      break;
  }
}
bool pidposition(long pidtarget) {
  float ppos = 0.1;
  float ipos = 0.0;
  float dpos = 0.0;

  long error = pidtarget - count;
  uint16_t adjeffort = ppos * error; //just p for now, I and D are for losers (and better tuned systems)
  adjeffort = abs(max(min(100, adjeffort), 0));
  if (error >= 0) {
    reverse(adjeffort);
  }
  else {
    forward(adjeffort);
  }
  if (abs(error) < 100) {
    return true;
  } else {
    return false;
  }

}

/**********************************************************************************************************************

                                                        INTERRUPT SERVICE ROUTINES


 **********************************************************************************************************************/

//ISRs split up for each hall-effect latch sensor to decrease processing time within the ISR and allow I2C to work every time without interruption

/**
   ISR for encoder 1 - reads registers instead of digital read for increased speed and increments/decrements a count variable
*/
void isr1() {
  uint8_t encread1 = PIND >> 2 & 0x01;
  uint8_t encread2 = PIND >> 3 & 0x01;  //get the two bit encoder read
  if (encread1 == encread2) {
    count++;
  }
  else {
    count--;
  }
}

/**
   ISR for encoder 2 - reads registers instead of digital read for increased speed and increments/decrements a count variable
*/
void isr2() {
  uint8_t encread1 = PIND >> 2 & 0x01;
  uint8_t encread2 = PIND >> 3 & 0x01;//get the two bit encoder read
  if (encread1 != encread2) {
    count++;
  }
  else {
    count--;
  }
}

/**********************************************************************************************************************

                                                    CURRENT SENSOR FUNCTIONS

 **********************************************************************************************************************/

/**
   Function to set the motorCurrent variable to the current sensor reading and check if it is stalled
*/
void readCurrent() {
  motorCurrent = analogRead(currentRead);
  // motorstalled=true;
  if (motorCurrent > 400) {
    motorstalledup = true;
  }
  else if (motorCurrent > 390) { //if the current reading is above the preset stall current value, brake the motor
    motorstalleddown = true;
  } else {
    motorstalleddown = false;
    motorstalledup = false;
  }
}

/**
   Function to home the cables using the current threshold
   Once homed, the motors reverse to limit current
   @param currentthreshold - the float current threshold in A
*/
void homeCables(float currentthreshold) {
  if (motorCurrent >= currentthreshold) {
    reverse(150);
  }
}

/**********************************************************************************************************************

                                                   DRIVING FUNCTIONS

 **********************************************************************************************************************/

/**
   This function drives the motors forward
   @param speed - the integer speed of the motor
*/
void forward(int speed) {
  analogWrite(INPUT1, 0);
  analogWrite(INPUT2, speed);
}

/**
   This function drives the motors reverse
   @param speed - the integer speed of the motor
*/
void reverse(int speed) {
  analogWrite(INPUT1, speed);
  analogWrite(INPUT2, 0);
}

/**
   This function stops the motors
*/
void brake() {
  analogWrite(INPUT1, 255);
  analogWrite(INPUT2, 255);
}



/**
   This function calculates PID for the motor speed
   @param error - the given error
   @return result - an integer clamped value for the speed of the motor
*/
int calcPID(int error) {
  result = abs(error * kp);
  if (error < 0) {
    result -= result;
  }
  else {
    result += result;
  }
  result = max(min((result), 200), 0);
  return result;
}

/**********************************************************************************************************************

                                                    I2C Functions


 **********************************************************************************************************************/

/**
   Callback function upon receiving a request for data via I2C from master
   This will request a set number of bytes as a message that will be formed for interpretation by the mainboard
*/
void requestEvent() {
  //split the int encoder count into multiple bytes
  data[0] = (count >> 8) & 0xFF;
  data[1] = count & 0xFF;
  data[2] = motorCurrent;
  data[3] = motSpeed;
  Wire.write(data, 4);
}

/**
   callback function for recieving messages and setting the appropriate I2C status
*/
void msgEvent(int numBytes) {
  // I2CFlag = true;
  while (Wire.available() > 0) { // loop through all but the last
    int x = Wire.read(); // receive byte as a character
    //    if (x>127){
    //      x = 256-x;
    //      x*=-1;
    //    }
    I2Cstatus = x;
  }
}

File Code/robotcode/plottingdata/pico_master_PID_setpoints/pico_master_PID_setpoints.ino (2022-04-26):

/**
   Uploaded to Mainboard - Handles I2C communication between smart motor driver boards, WiFi communication between external esp
**/


#include <Wire.h> //include Wire.h library
#include <esp_now.h> //ESP-Wifi comms
#include <WiFi.h>
#include <Math.h>


/**
    Wheel Addresses
    1,2,3 - Drive Wheels
    4,5,6 - Cable Motors
    7 - Lead Screw Motor
*/

/**********************************************************************************************************************

                                                    VARIABLES + DEFINITIONS


 **********************************************************************************************************************/


//ESP-NOW Variables
uint8_t broadcastAddress1[] = {0x98, 0xCD, 0xAC, 0x61, 0x58, 0xAC}; //replace with the MAC Address of your ESP

typedef struct data_struct { //data struct to send to the receiver/external ESP containing address, current sensor, and encoder data
  // data types must match data struct sent from external ESP
  int smdAddress;
  int currentData;
  int encoderData;
} data_struct;

typedef struct data_struct_rec { //data struct to receive wifi commands from the external ESP  - must match data struct sent from external ESP
  int s;
  int theta;
  int phi;
} data_struct_rec;

data_struct test; //create instance of sending struct to be populated with data
data_struct_rec myData; //create instance of receiving struct


//data variables from smart motor drivers
int count = 0; //encoder count
char current = 0; //current reading
const int vRef = 3.3; //reference logic level voltage
const int senseResistor = 0.5; //current sense resistor in Ohms
byte enc1, enc2; //encoder variables
const int encTicksPerRev = 12; //encoder ticks per revolution
const float motorGearRatio = 298.00; //gear ratio on high strength N20 motors

//cable variables
int cablelenraw = 0; //unused
float cablelenadj = 0; //unused
//cable length and encoder count variables
float l1 = 0;
float l2 = 0;
float l3 = 0;
int c1, c2, c3;

const float drumdiameter = 0.275; //Diameter of the winch drums for the cable motors - inches i guessed
const float origlength = 3.35; //original length of the Yoshimura module

const float r = 2.04 ; //radius of module
const float L0 = 1;//shortest length of module in inches

float s, theta, phi; //arc length, bending angle, bending directions - from soft robotics lab paper
const float d = 1.0; //distance from the center of mounting plate to cable attachment point - inches
const float n = 1.0; //number of yoshimura module sections - for our purposes we only use one robot

int encL1, encL2, encL3 = 0;
float l1Setpoint, l2Setpoint, l3Setpoint = 0.0;

byte data[2]; //I2c data array
byte inputcount1, inputcount2;
int inputcount = 0;
int motspeed = 0; 



/**********************************************************************************************************************

                                                         SETUP + LOOP


 **********************************************************************************************************************/

void setup()
{
  Wire.begin(); // I2C communication begin
  Serial.begin(9600); // The baudrate of Serial monitor is set in 9600 - lower baudrates work best with motor driver modules
  while (!Serial); // Waiting for Serial Monitor to initialize
  Serial.println("\nI2C Scanner");

  //  //Set device as a Wi-Fi Station
  //  WiFi.mode(WIFI_STA);
  //
  //  //Init ESP-NOW
  //  if (esp_now_init() != ESP_OK) {
  //    Serial.println("Error initializing ESP-NOW");
  //    return;
  //  }

  // Once ESPNow is successfully Init, we will register for recv CB to
  // get recv packer info
  //sp_now_register_recv_cb(OnDataRecv);

  //run once on startup to verify SAMIs connected
  findDevices();

  //register callback function to be called when a message is sent
  // esp_now_register_send_cb(OnDataSent);

  // register peer
  //  esp_now_peer_info_t peerInfo;
  //  peerInfo.channel = 0;
  //  peerInfo.encrypt = false;
  //
  //  // register first peer
  //  memcpy(peerInfo.peer_addr, broadcastAddress1, 6);
  //  if (esp_now_add_peer(&peerInfo) != ESP_OK) {
  //    Serial.println("Failed to add peer");
  //    return;
  //  }
}
long lastTime = 0;
uint16_t current7 = 0;
void loop() {
  //try just sending to setpoint and then asking again
  sendIntegerMsg(0x07, 0);
  delay(5000);
  sendIntegerMsg(0x07, 4000);
  for (int i = 0; i < 200; i++) {
    requestData(0x07, 6);
    Serial.print("Time: ");
    Serial.print(millis());
    Serial.print('\t');
    Serial.print('\t');
    Serial.print("Position : ");
    Serial.print(c1);
    Serial.print('\t');
    Serial.print("speed: ");
    Serial.println(motspeed);
    delay(10);
  }


  //  //  //timing based setting setpoint and then requesting data back to plot
  //  sendIntegerMsg(0x07, 0);
  //  delay(6000);
  //  for (uint16_t posSetpoint = 0; posSetpoint <2000; posSetpoint += 100) {
  //    Serial.print("Time: ");
  //    Serial.print(millis());
  //    Serial.print('\t');
  //    Serial.print("Setpoint:");
  //    Serial.print('\t');
  //    int set = (posSetpoint);
  //    Serial.print(-set);
  //    sendIntegerMsg(0x07, -set);
  //    delay(500);
  //    Serial.print('\t');
  //    Serial.print("Position : ");
  //    requestData(0x07, 6);
  //    Serial.print(c1);
  //    Serial.print('\t');
  //    Serial.print("Current: ");
  //    Serial.println(current7);
  //    delay(500);
  //  }
  //  sendIntegerMsg(0x07, 1000);
  //  delay(5000);
  //  requestData(0x07, 6);
  //  Serial.println(c1);
  //  sendIntegerMsg(0x07, 0);
  delay(10000);
}


/**********************************************************************************************************************

                                                        I2C FUNCTIONS


 **********************************************************************************************************************/
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

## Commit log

2021-11-08 Pushing local code
    [triple_motor_control_ls7366r_i2c_cur_sensing_atmeg.componentinfo.xml, triple_motor_control_with_ls7366r_and_cur_sensing_atmega32u4.componentinfo.xml]
2021-12-04 added i2c and uart
    [triple_motor_control_ls7366r_i2c_cur_sensing_atmeg.componentinfo.xml, triple_motor_control_with_ls7366r_and_cur_sensing_atmega32u4.componentinfo.xml]
2021-12-05 Got Wifi communication to work - current protocol: external TinyPICO sends a WiFi command, mainboard receives it and requests information from motor driver via I2C, motor driver returns data on I2C a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
2021-12-06 added a few clarifying comments on i2c and wifi functions
2021-12-07 can now send data through serial monitor and receive a response through our circuit board loop
2021-12-07 Added prelim motor pwm code - pwm output works on motor driver pads
2021-12-16 SAMI Board motor moves forward and reverse (sometimes)!!!!
    [slave_sender.ino]
2022-01-19 i2c stuff
2022-01-19 working switch statement
2022-01-20 i hate it here please free me from this i2c hell
2022-01-21 changes i think that'll make multiple data over i2c work
2022-01-21 encoder and current sensor work
2022-01-21 pico sender is the one we want with the controller
2022-01-31 going to test why motor wont reverse today but i dont think i've pushed recently
    [slave_sender.ino]
2022-01-31 motors go forward and back
2022-02-02 working on the stall protection... seems like it works mostly
    [SAMI_nonreversed.ino]
2022-02-05 figured out buttons need to ask yoni questions my brain is no longer working
    [pico_sender.ino]
2022-02-05 i think cables and lead screw are in
2022-02-10 current readings work now, fixing encoders
    [pico_master.ino, pico_sender.ino]
2022-02-11 the encoders fuck
2022-02-11 the encoders work and im fucking pissed about it
2022-02-13 mostly added pid. not sure i would test this yet....
2022-02-13 the encoders now work without an ISR
2022-02-16 cables are a thing now till i broke it. PID still tbd need to test
    [SAMI_nonreversed.ino, pico_master.ino]
2022-02-16 cables fixed, can go up and down, and are slower
    [SAMI_nonreversed.ino, pico_master.ino, pico_sender.ino]
2022-02-17 PID is somewhat working i guess
2022-02-18 the lead screw opens and closes the proper amount with current feedback
2022-02-25 PID speed actually works (it's really just a p controller)...
2022-02-28 inverse kinematics calculations are in but not tested, need to measure the constants... ?
2022-03-01 pico_sender reorganized - moving onto sami non reverse
    [pico_sender.ino]
2022-03-01 organized SAMI non reversed
    [SAMI_nonreversed.ino]
2022-03-02 inverse_kinematics_esp_sender -> changed sending struct to send k, s, phi to pico. Removed controller functionality. Added Serial peek logic in loop to read from Serial monitor, taking inputs one at 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
    inverse_kinematics_pico_master -> changed receiving struct, renamed inverse kin to forward kin, added forward kin calculations. Forward kin automatically calculates on receiving wifi data from extern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
2022-03-04 sending change in encoder counts required to achieve inverse kinematics from input e-e variable calculations via I2C
2022-03-04 SAMI boards should relay information back to the pico master about the input encoder counts
2022-03-04 Flashed Motor 6 with new IK code - can't get the data that we send back from the motor - negative numbers dont seem to work and positive numbers are just slightly off
2022-03-22 fixed some ik math
    [inverse_kinematics_pico_master.ino]
2022-03-29 i realized i was messing up the integral accumulator and fixed it yay
    [kinematics_SAMI_nonreversed.ino, pico_master_PID_setpoints.ino]
2022-03-31 changed PID coeff for unloaded motor following position trajectory
2022-04-08 changed some stuff to fix bad cable behavior
    [pico_master.ino, pico_sender.ino]
2022-04-12 current sensor bunk
2022-04-14 trying some new stuff with the current sensor later today
2022-04-26 mechanical + electrical files
    [4 to 3.5 concentric reducer.SLDPRT, 4262T350_PRECISION FLANGED BALL BEARING.SLDPRT, 57155K427_Stainless Steel Ball Bearing.SLDPRT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]
2022-04-26 Reorganized files, added & compressed ppt
    [4 to 3.5 concentric reducer.SLDPRT, 4262T350_PRECISION FLANGED BALL BEARING.SLDPRT, 57155K427_Stainless Steel Ball Bearing.SLDPRT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]
2022-04-26 Adding PCB tracking, requirements testing, and project proposal to documents folder
    [Cost Analysis.xlsx, PCB Boards Ordering Tracking.xlsx, Requirements + Testing Matrix.xlsx]
2022-04-28 replacing smart motor driver diagram
2022-04-28 replacing smart motor driver diagram again

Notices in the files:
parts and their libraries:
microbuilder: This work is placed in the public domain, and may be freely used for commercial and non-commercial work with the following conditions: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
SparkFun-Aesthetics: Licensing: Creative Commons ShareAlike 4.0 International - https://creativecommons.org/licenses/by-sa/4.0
